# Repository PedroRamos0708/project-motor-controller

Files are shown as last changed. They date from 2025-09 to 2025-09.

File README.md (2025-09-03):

# Projeto de Controle com Microcontrolador

## Descrição
Este projeto foi desenvolvido como parte de um desafio de hardware.
O objetivo é criar um sistema embarcado capaz de:
* Receber um sinal externo de 12 V ativo em nível baixo.
* Acionar um motor DC 5 V / 1 A por 10 segundos.
* Enviar mensagens de status via UART RS232.
* Ser alimentado por uma fonte de 9 a 24 VDC, com proteções contra inversão de polaridade e surtos.

## Especificações de Hardware
* Microcontrolador: ATmega328P + botão de reset.
* Fonte de alimentação: regulador LM2596 (9–24 VDC para 5 V).
* Motor: 5 V / 1 A, acionado via MOSFET canal N, com fusível de proteção.
* Proteções:
  * Fusível resetável (PTC).
  * Diodo Schottky (SS34).
  * Diodo TVS (SMBJ33A).
* Interface de entrada: optoacoplador para isolamento do sinal de 12 V.
* Comunicação serial: MAX3232 para RS232.
* Sinalização de placa energizada: LED

## Firmware
O firmware em C/C++ (pronto para compilação no ARDUINO IDE) realiza:
1. Leitura do sinal externo via optoacoplador.
2. Acionamento do motor por 10 segundos.
3. Envio de mensagens de status na UART.

## Arquivos Gerados
* Esquemático em PDF.
* PCB desenhada no KiCad 9.
* Arquivos Gerber e Drill files para fabricação.
* Pick and Place (PnP) para montagem.
* BOM (Bill of Materials) para compra dos componentes.
* Arquivos de projeto editáveis da placa e esquematico (.kicad_pcd e _sch)

## Como usar
1. Alimente a placa com 9 a 24 VDC no conector J1 (pino interno VCC e externo GND) através de fonte externa;
2. Conecte o sinal externo de 12 V no borne J3 (pino 1 : GND, pino 2 : 12V) para habilitação do motor;
3. Conecte o motor DC 5 V / 1 A no borne J4 (pino 1 : +, pino 2 : GND);
4. Utilize a porta RS232 (Conector db9 J2) para monitorar as mensagens do sistema.

## Tecnologias Utilizadas
* KiCad 9 → desenvolvimento do esquemático e PCB.
* Arduino IDE → programação do microcontrolador.

## Autor
Projeto desenvolvido por Pedro Henrique Ramos, Engenheiro de Controle e Automação e técnico em eletroeletrônica.

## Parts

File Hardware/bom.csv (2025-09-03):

Reference | Qty | Value | DNP | Exclude from BOM | Exclude from Board | Footprint | Datasheet
C1,C3 | 2 | 22pF |  |  |  | Capacitor_THT:C_Disc_D4.3mm_W1.9mm_P5.00mm
C2,C4,C5,C6,C9,C12,C13,C15 | 8 | 100nF |  |  |  | Capacitor_THT:C_Disc_D4.3mm_W1.9mm_P5.00mm | ~
C7 | 1 | 220uF/16V |  |  |  | Capacitor_THT:CP_Radial_D8.0mm_P5.00mm | ~
C8 | 1 | 680uF |  |  |  | Capacitor_THT:CP_Radial_D13.0mm_P7.50mm | ~
C10,C11 | 2 | 1uF/10V |  |  |  | Capacitor_SMD:C_0805_2012Metric | ~
C14 | 1 | 100uF |  |  |  | Capacitor_THT:CP_Radial_D5.0mm_P2.50mm | ~
D1 | 1 | 1n5824 |  |  |  | Package_TO_SOT_THT:TO-220-2_Vertical | ~
D2 | 1 | SMBJ33A |  |  |  | Diode_SMD:D_SMB | ~
D3 | 1 | LED |  |  |  | LED_THT:LED_D5.0mm | ~
D4,D6 | 2 | SS34 |  |  |  | Diode_SMD:D_SMA | https://www.vishay.com/docs/88751/ss32.pdf
D5 | 1 | 1N5819 |  |  |  | Diode_THT:D_DO-41_SOD81_P10.16mm_Horizontal | http://www.vishay.com/docs/88525/1n5817.pdf
F1 | 1 | 2A |  |  |  | Fuse:Fuseholder_Clip-5x20mm_Bel_FC-203-22_Lateral_P17.80x5.00mm_D1.17mm_Horizontal | ~
J1 | 1 | Jack-DC |  |  |  | Connector_BarrelJack:BarrelJack_Horizontal | ~
J2 | 1 | DE9_Socket |  |  |  | Connector_Dsub:DSUB-9_Socket_Horizontal_P2.77x2.84mm_EdgePinOffset4.94mm_Housed_MountingHolesOffset4.94mm | ~
J3,J4 | 2 | Screw_Terminal_01x02 |  |  |  | TerminalBlock:TerminalBlock_Altech_AK300-2_P5.00mm | ~
L1 | 1 | 33uH |  |  |  | Inductor_THT:L_Radial_D12.5mm_P7.00mm_Fastron_09HCP | ~
Q1 | 1 | IRLZ44N |  |  |  | Package_TO_SOT_THT:TO-220-3_Vertical | http://www.irf.com/product-info/datasheets/data/irlz44n.pdf
R1 | 1 | 10K |  |  |  | Resistor_THT:R_Axial_DIN0207_L6.3mm_D2.5mm_P10.16mm_Horizontal | ~
R2 | 1 | 1k |  |  |  | Resistor_THT:R_Axial_DIN0207_L6.3mm_D2.5mm_P10.16mm_Horizontal | ~
R5 | 1 | 4k7 |  |  |  | Resistor_THT:R_Axial_DIN0207_L6.3mm_D2.5mm_P10.16mm_Horizontal | ~
R6,R8 | 2 | 10k |  |  |  | Resistor_THT:R_Axial_DIN0207_L6.3mm_D2.5mm_P10.16mm_Horizontal | ~
R7 | 1 | 100 |  |  |  | Resistor_THT:R_Axial_DIN0207_L6.3mm_D2.5mm_P10.16mm_Horizontal | ~
SW1 | 1 | SW_Push |  |  |  | Button_Switch_THT:SW_PUSH_6mm_H5mm | ~
TH1 | 1 | Thermistor_PTC |  |  |  | Fuse:Fuse_BelFuse_0ZRE0025FF_L9.6mm_W3.8mm | ~
U1 | 1 | ATmega328-P |  |  |  | Package_DIP:DIP-28_W7.62mm | http://ww1.microchip.com/downloads/en/DeviceDoc/ATmega328_P%20AVR%20MCU%20with%20picoPower%20Technology%20Data%20Sheet%2040001984A.pdf
U2 | 1 | LM2596T-5 |  |  |  | Package_TO_SOT_THT:TO-220-5_P3.4x3.7mm_StaggerOdd_Lead3.8mm_Vertical | http://www.ti.com/lit/ds/symlink/lm2596.pdf
U3 | 1 | MAX3232 |  |  |  | Package_SO:JEITA_SOIC-16_3.9x9.9mm_P1.27mm | https://datasheets.maximintegrated.com/en/ds/MAX3222-MAX3241.pdf
U4 | 1 | PC817 |  |  |  | Package_DIP:DIP-4_W7.62mm | http://www.soselectronic.cz/a_info/resource/d/pc817.pdf
Y1 | 1 | 16MHz |  |  |  | Crystal:Crystal_HC49-4H_Vertical | ~

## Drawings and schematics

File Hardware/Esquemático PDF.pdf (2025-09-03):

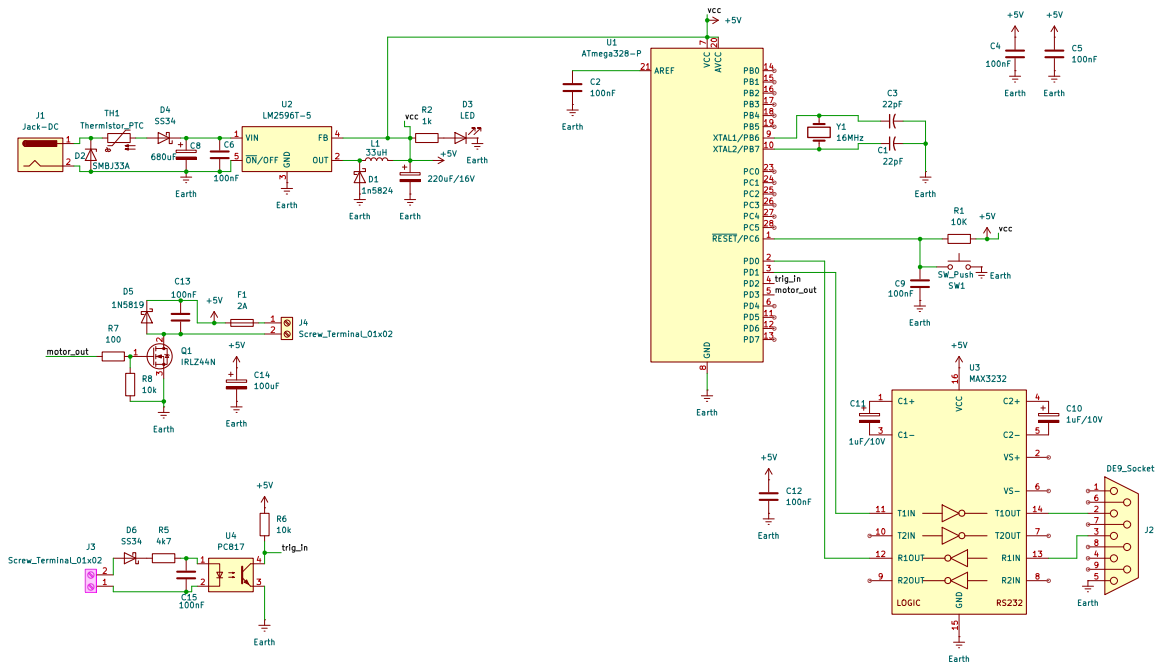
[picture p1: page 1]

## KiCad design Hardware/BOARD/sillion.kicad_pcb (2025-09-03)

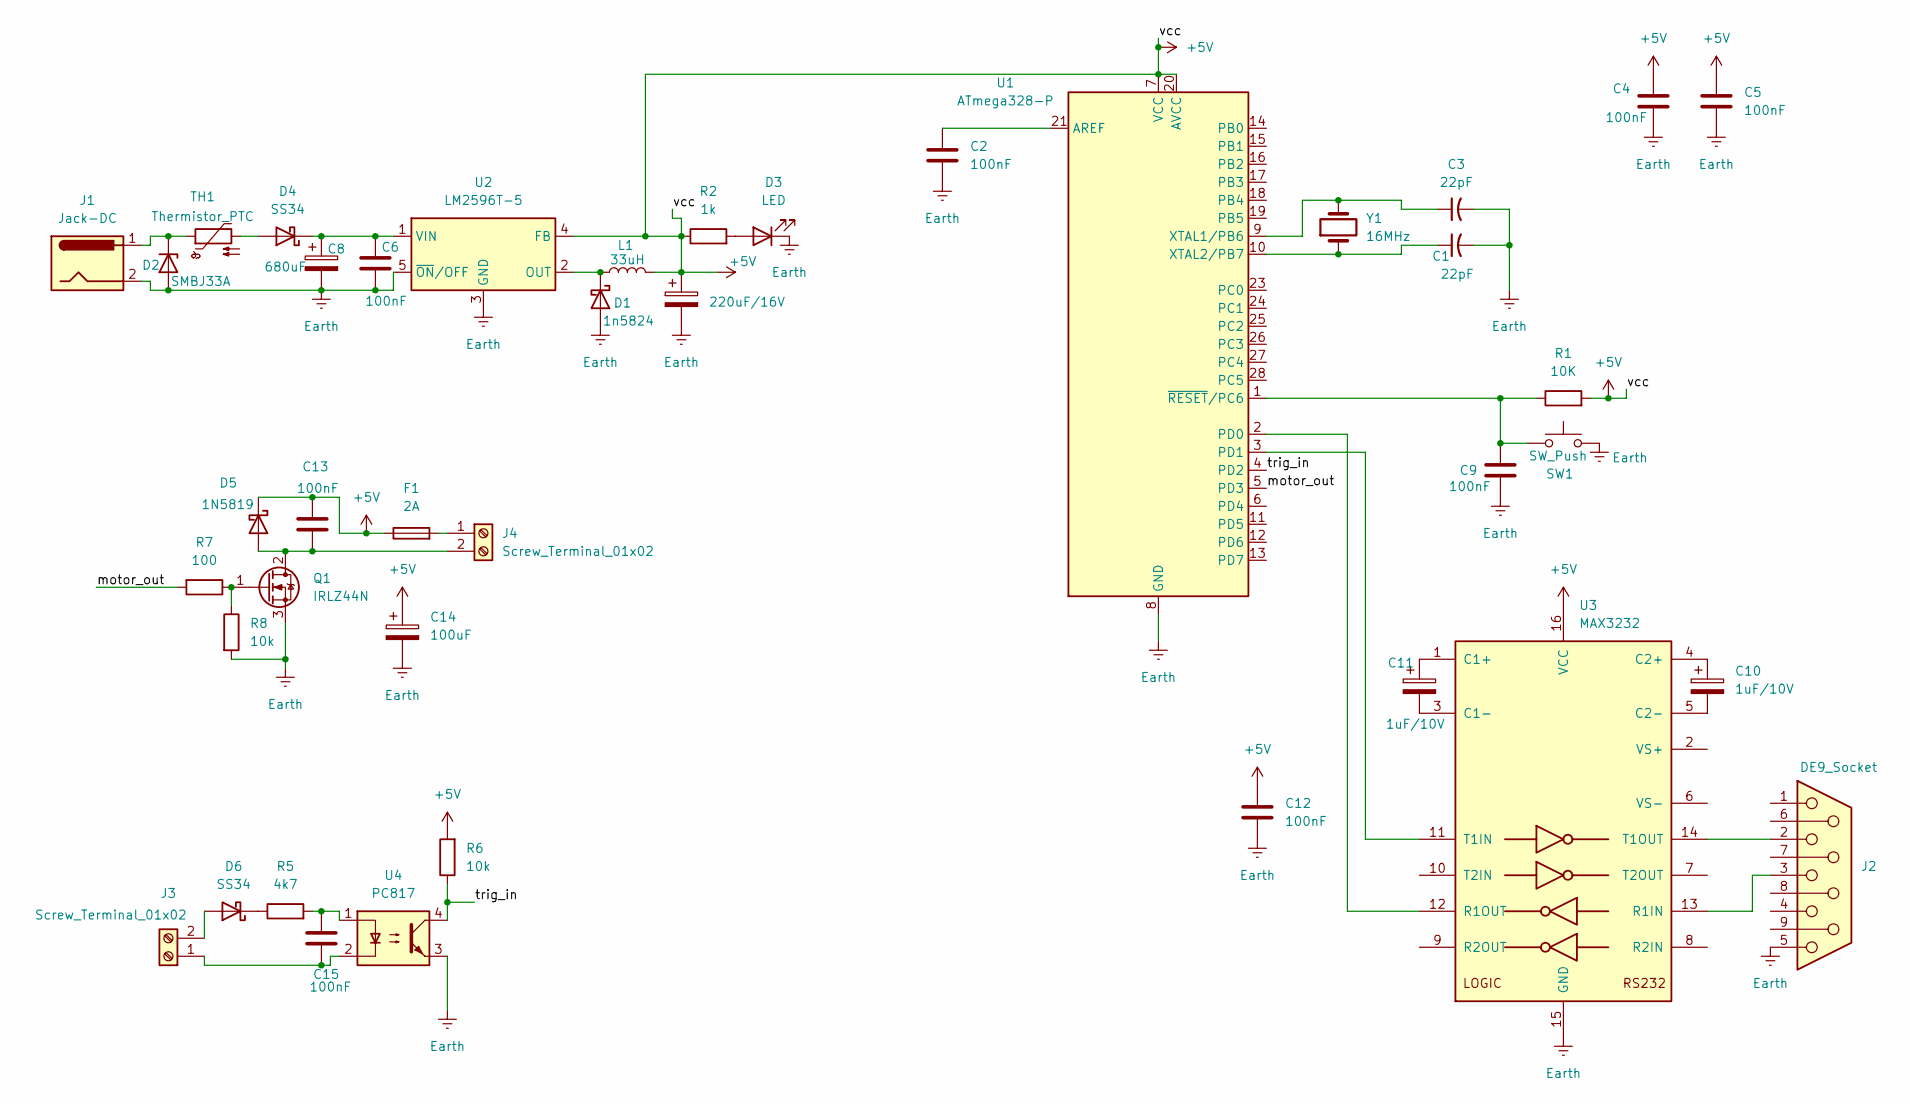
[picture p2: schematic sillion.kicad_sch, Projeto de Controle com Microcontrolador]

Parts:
C1, C3: 22pF; C_Disc_D4.3mm_W1.9mm_P5.00mm
C2, C4, C5, C6, C9, C12, C13, C15: 100nF; C_Disc_D4.3mm_W1.9mm_P5.00mm
C7: 220uF/16V; CP_Radial_D8.0mm_P5.00mm
C8: 680uF; CP_Radial_D13.0mm_P7.50mm
C10, C11: 1uF/10V; C_0805_2012Metric
C14: 100uF; CP_Radial_D5.0mm_P2.50mm
D1: 1n5824; TO-220-2_Vertical
D2: SMBJ33A; D_SMB
D3: LED; LED_D5.0mm
D4, D6: SS34; D_SMA
D5: 1N5819; D_DO-41_SOD81_P10.16mm_Horizontal
F1: 2A; Fuseholder_Clip-5x20mm_Bel_FC-203-22_Lateral_P17.80x5.00mm_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
J1: Jack-DC; BarrelJack_Horizontal
J2: DE9_Socket; DSUB-9_Socket_Horizontal_P2.77x2.84mm_EdgePinOffset4.94mm_H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
J3, J4: Screw_Terminal_01x02; TerminalBlock_Altech_AK300-2_P5.00mm
L1: 33uH; L_Radial_D12.5mm_P7.00mm_Fastron_09HCP
Q1: IRLZ44N; TO-220-3_Vertical
R1: 10K; R_Axial_DIN0207_L6.3mm_D2.5mm_P10.16mm_Horizontal
R2: 1k; R_Axial_DIN0207_L6.3mm_D2.5mm_P10.16mm_Horizontal
R5: 4k7; R_Axial_DIN0207_L6.3mm_D2.5mm_P10.16mm_Horizontal
R6, R8: 10k; R_Axial_DIN0207_L6.3mm_D2.5mm_P10.16mm_Horizontal
R7: 100; R_Axial_DIN0207_L6.3mm_D2.5mm_P10.16mm_Horizontal
SW1: SW_Push; SW_PUSH_6mm_H5mm
TH1: Thermistor_PTC; Fuse_BelFuse_0ZRE0025FF_L9.6mm_W3.8mm
U1: ATmega328-P; DIP-28_W7.62mm
U2: LM2596T-5; TO-220-5_P3.4x3.7mm_StaggerOdd_Lead3.8mm_Vertical
U3: MAX3232; JEITA_SOIC-16_3.9x9.9mm_P1.27mm
U4: PC817; DIP-4_W7.62mm
Y1: 16MHz; Crystal_HC49-4H_Vertical

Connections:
+5V: C4.1, C5.1, C7.1, C12.1, C13.1, C14.1, D5.1 (K), F1.1, L1.2, R1.2, R2.1, R6.2, U1.7 (VCC), U1.20 (AVCC), U2.4 (FB), U3.16 (VCC)
/motor_out: R7.2, U1.5 (PD3)
/trig_in: R6.1, U1.4 (PD2), U4.4
Earth: C1.2, C2.2, C3.2, C4.2, C5.2, C6.2, C7.2, C8.2, C9.2, C12.2, C14.2, D1.2 (A), D2.2 (A), D3.1 (K), J1.2, J2.5, Q1.3 (S), R8.2, SW1.2, U1.8 (GND), U1.22 (GND), U2.3 (GND), U2.5 (~ON/OFF), U3.15 (GND), U4.3
unnamed: C15.1, R5.2, U4.1
unnamed: D1.1 (K), L1.1, U2.2 (OUT)
unnamed: D2.1 (K), J1.1, TH1.1
unnamed: D3.2 (A), R2.2
unnamed: D4.2 (A), TH1.2
unnamed: C6.1, C8.1, D4.1 (K), U2.1 (VIN)
unnamed: C13.2, D5.2 (A), J4.2, Q1.2 (D)
unnamed: D6.2 (A), J3.2
unnamed: D6.1 (K), R5.1
unnamed: C15.2, J3.1, U4.2
unnamed: F1.2, J4.1
unnamed: Q1.1 (G), R7.1, R8.1
unnamed: C2.1, U1.21 (AREF)
unnamed: U1.2 (PD0), U3.12 (R1OUT)
unnamed: U1.3 (PD1), U3.11 (T1IN)
unnamed: C3.1, U1.9 (XTAL1/PB6), Y1.2
unnamed: C1.1, U1.10 (XTAL2/PB7), Y1.1
unnamed: C9.1, R1.1, SW1.1, U1.1 (~RESET/PC6)
unnamed: C11.1, U3.1 (C1+)
unnamed: C11.2, U3.3 (C1-)
unnamed: C10.1, U3.4 (C2+)
unnamed: C10.2, U3.5 (C2-)
unnamed: J2.3, U3.13 (R1IN)
unnamed: J2.2, U3.14 (T1OUT)

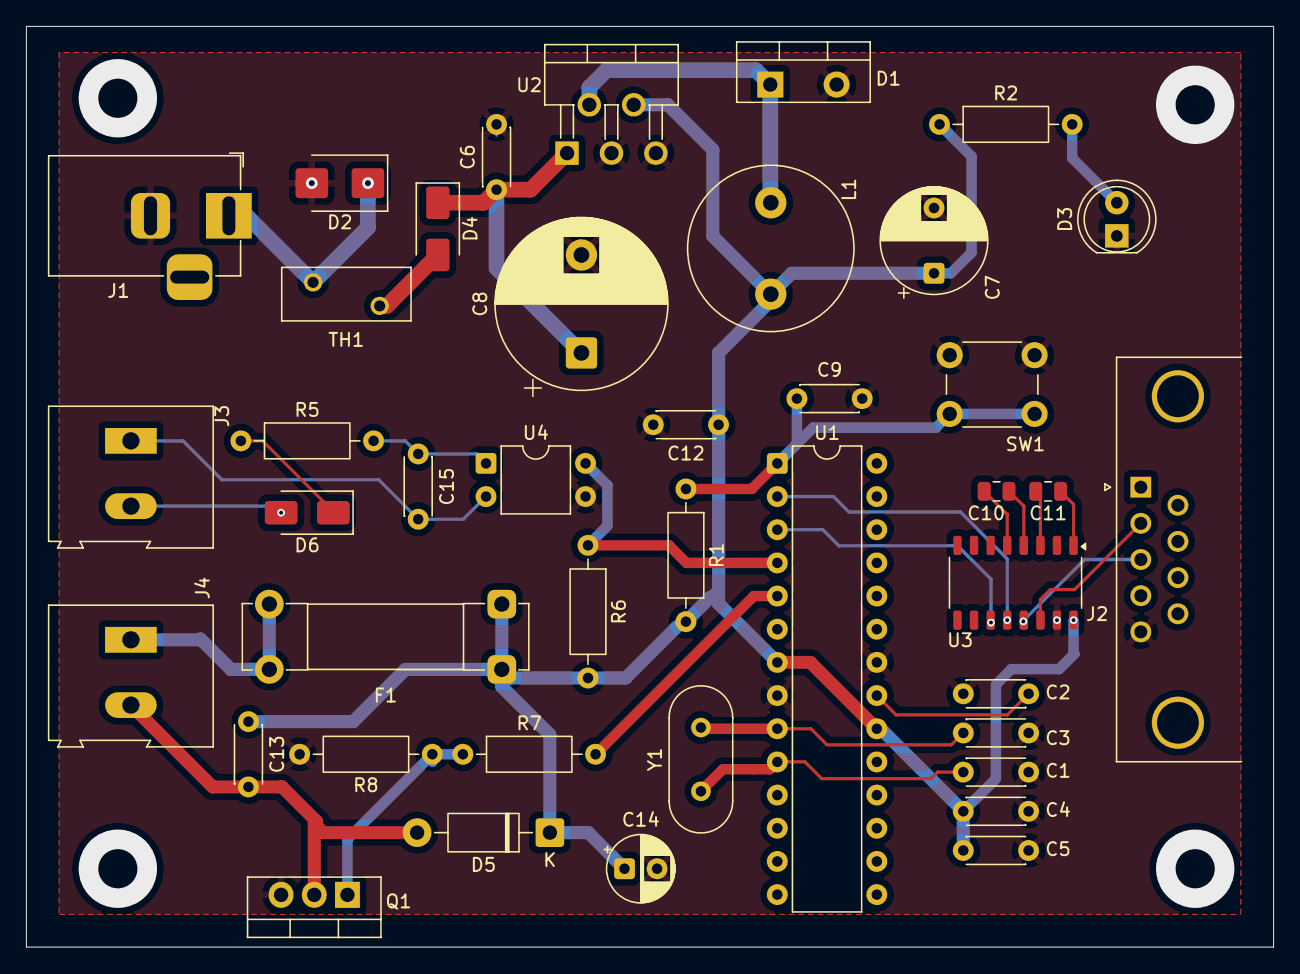
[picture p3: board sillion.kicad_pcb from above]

Board: 2 copper layers, 95.5 x 70.5 mm, 41 parts (0 on the bottom side), 28 nets.

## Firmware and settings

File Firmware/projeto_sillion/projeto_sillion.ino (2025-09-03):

const int motorPin   = 3; //declaração de variáveis
const int triggerPin = 2; 

void setup() {
  pinMode(motorPin, OUTPUT); // setando o pino PD3 como saída
  pinMode(triggerPin, INPUT_PULLUP); //setando o PD2 como entrada
  Serial.begin(9600); // inicializando a comunicação serial
  }

void loop() {
  if (digitalRead(triggerPin) == LOW) { // se a entrada digital interpretar sinal 0V
    Serial.println("Motor ON"); //envia a mensagem no serial
    digitalWrite(motorPin, HIGH);  // envia 5V para a saída PD3
    delay(10000);  // motor ligado por 10 segundos
    digitalWrite(motorPin, LOW);   // desativa o chaveamento do MOSFET
    Serial.println("Motor OFF"); //envia nova mensagem no serial
    delay(200); // espera
  }
}
